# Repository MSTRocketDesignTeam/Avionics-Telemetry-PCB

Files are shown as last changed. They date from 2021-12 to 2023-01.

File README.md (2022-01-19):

View this project on [CADLAB.io](https://cadlab.io/project/24983). 

# Overview

This repository contains the PCB files for the main Rocket Telemetry project.

## Purpose and Motivation
This project aims to create flight-rated PCBs that can collect information about the team's rockets as they are launched.

The primary impetus for this project is to develop a student-designed solution to keep the team from losing rockets. This means that these boards must contain and interface with the electronics required to track and analyze a rocket mid-flight and indicate the rocket landing site location to the team back at the launch site to aid in recovery efforts.

The second purpose of this board is to collect and stream performance data about the rocket during all stages of its flight. This data will come from onboard sensors that measure the rocket’s acceleration, altitude, speed, orientation, etc. This will initially only be stored onboard the rocket, with the long-term goal of feeding a real-time 3D model simulation of the rocket’s flight to the team at the launch site. It should also be a goal to include future capabilities for interfacing with external sensors, such as thermocouples, pressure transducers, cameras, and more.

## Inspirations

Initial developments of this board are to be a direct replacement for a Telemetrum V3, with features and design optimizations to be implemented in future revisions.

A [Telemetrum V3](https://altusmetrum.org/TeleMetrum/) is an amateur rocketry telemetry solution from [Altus Metrum](https://altusmetrum.org/index.html).

[Signal](https://bps.space/signal/) from [BPS.Space](https://bps.space/) is a flight computer first and a data collection solution second. It is designed to stream data to the ground station, although it is likely insufficient for the large 10-30k ft class rockets that our team constructs.

An excellent KiCAD tutorial around making a small thumb-drive-sized PCB with an STM32, RF, and USB components: [here on YouTube by Phil's Lab](https://www.youtube.com/watch?v=14_jh3nLSsU) and is an excellent tutorial on using circuit design software and the process/approach you go through making something like this. Highly recommended to watch and maybe take some notes on. This is a solid start for our telemetry board.

# Features

#### Physical

* Expected Size: 53 x 69 mm (Arduino Uno)
* Best Size: Around 75 x 25 mm if possible
* Thin/Long is better than Square
* Rectangular shape w/ rounded edges
* Screw Mounting Holes

#### Primary Components

* STM32 Family Microcontroller
* 900MHz Radio Module
* GPS Receiver
* External RF Antenna Connector

#### Sensors

* Accelerometer
* Magnetometer
* Barometer
* Gyroscope
* Temperature

#### Data

* Flash Storage Chip for inflight capture
* Micro SD Card Reader for postflight storage
* Debugging/programming header

#### Power

* Connection to LiPo Packs
* Coin Cell/Capacitor Battery Backup
* No charge controller
* Low-power mode preflight

# Companion Documentation

[Telemetry Board R&D Documentation Folder - Google Drive](https://drive.google.com/drive/folders/1-Ft9_IYGoKeQ8SOpWUMPCNhws5y90gv3?usp=sharing)

[Component Comparison - Google Sheet](https://docs.google.com/spreadsheets/d/1QPZUW1DP2L5ciMKxbgeHV3uC0-h4SxSqm0nYhaIsA54/edit?usp=sharing)

[Telemetrum V3 Features and Components - Google Doc](https://docs.google.com/document/d/1UKlisEx7MZwDFethEzJ8d39NXyabVl6lI_5ZflczvP4/edit?usp=sharing)

[Telemetry Board Requirement Brainstorm - Google Doc](https://docs.google.com/document/d/1sqFQGxX3MVceV2B7MoNJb_ZmXdHjXhyEQbpknLjsYw0/edit?usp=sharing)

[Telemetry Notepad - Google Doc](https://docs.google.com/document/d/1K5M_XsDRmasx09W511Fg23m5dxfRa6N_FNR6dFqZZKQ/edit?usp=sharing)

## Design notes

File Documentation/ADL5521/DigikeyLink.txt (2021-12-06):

https://www.digikey.com/en/products/detail/analog-devices-inc/ADL5521ACPZ-R7/2033820

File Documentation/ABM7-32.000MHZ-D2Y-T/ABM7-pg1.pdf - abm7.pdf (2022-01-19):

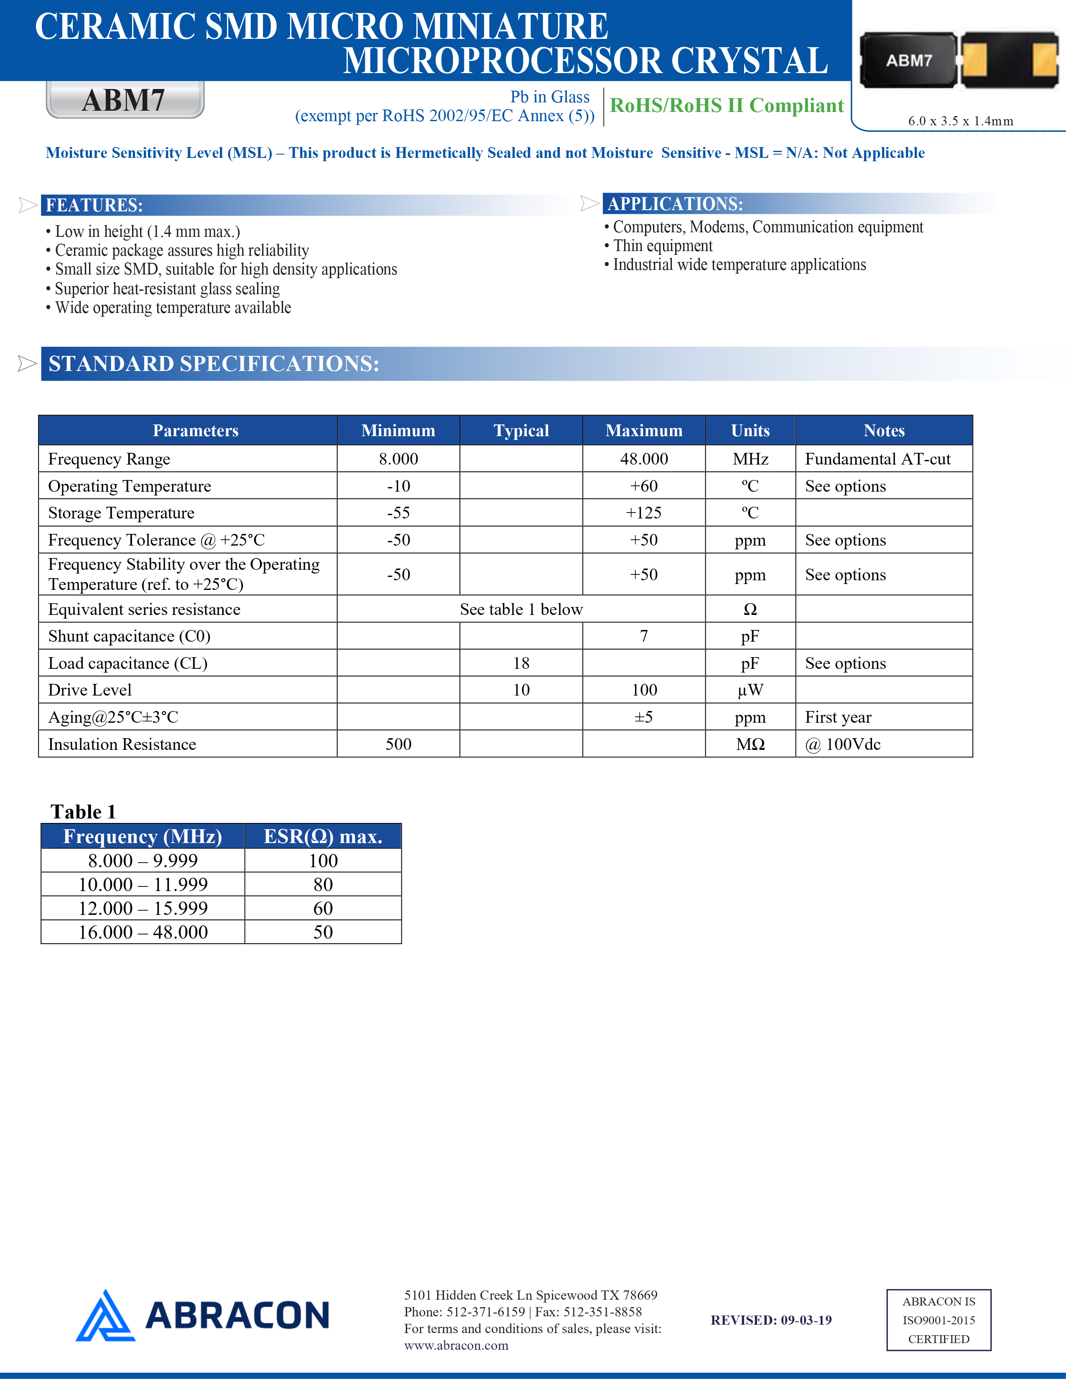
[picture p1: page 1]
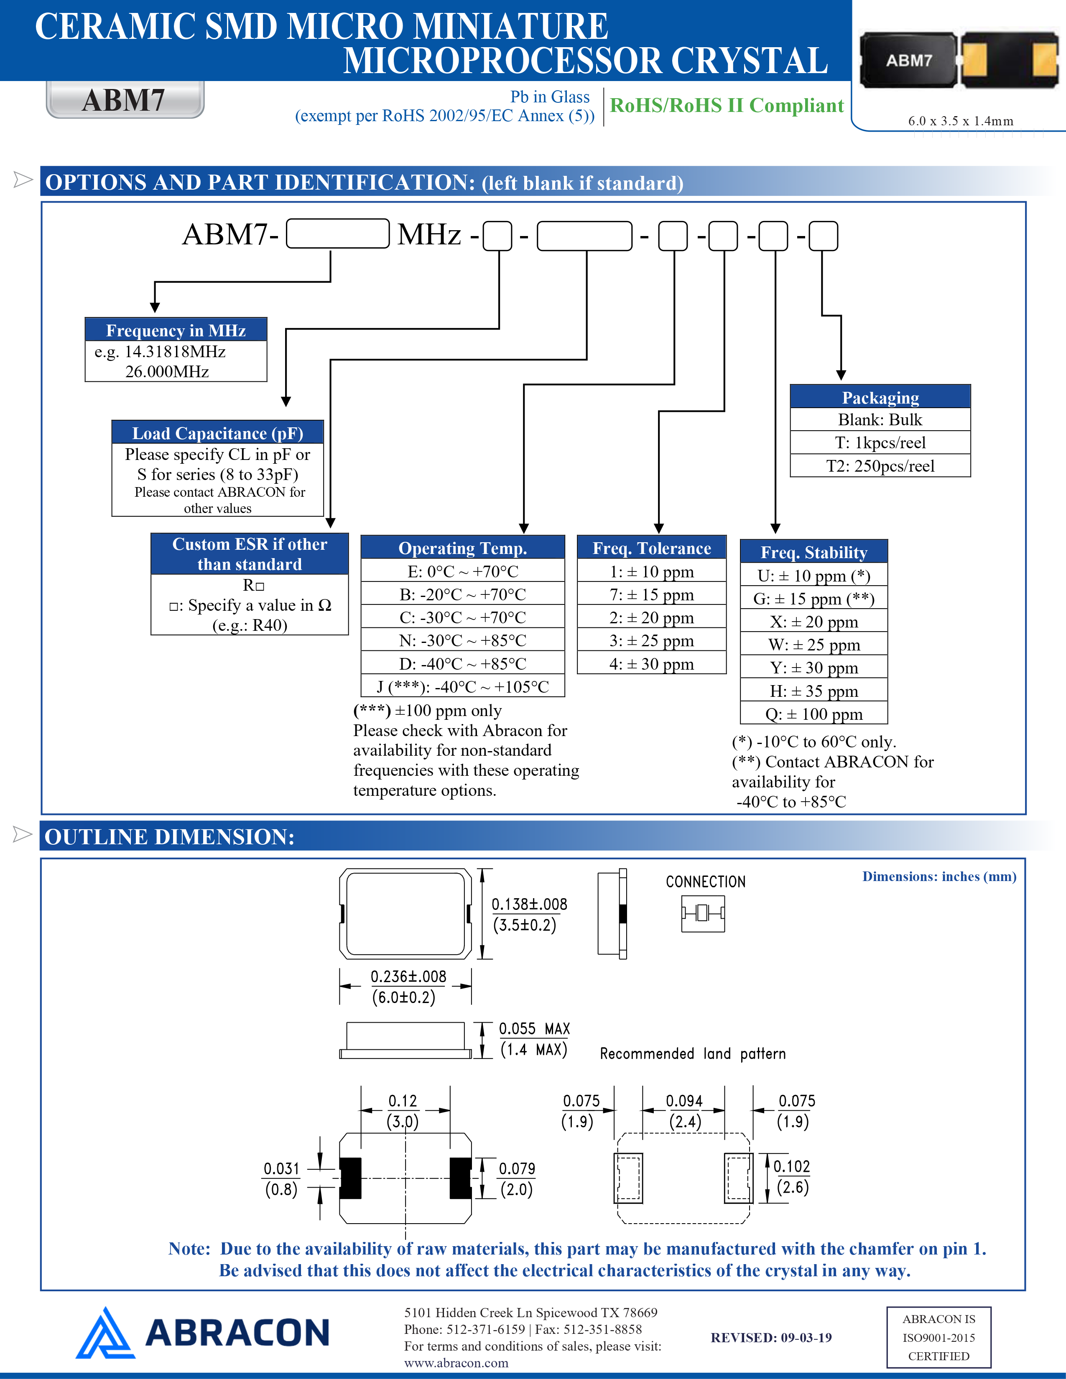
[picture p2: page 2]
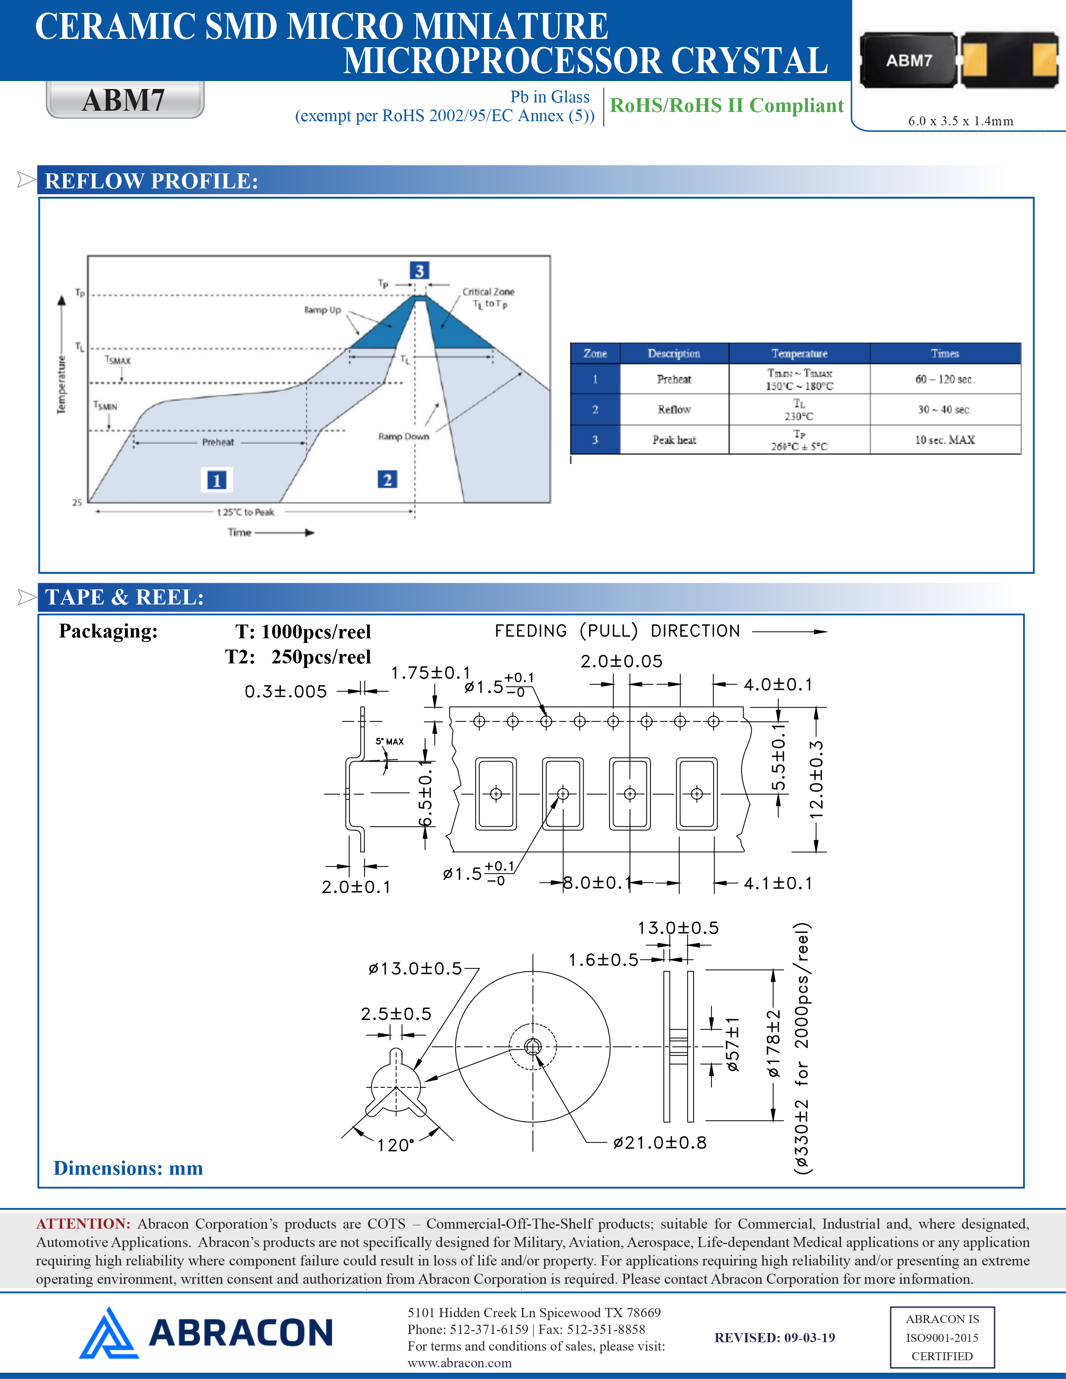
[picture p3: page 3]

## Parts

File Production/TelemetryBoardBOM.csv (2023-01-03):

Comment | Designator | Footprint | LCSC
2.4pF | C11 | Capacitor_SMD:C_0402_1005Metric | C123475
100nF | C12 | Capacitor_SMD:C_0402_1005Metric | C307331
0.1uF | C13 | Capacitor_SMD:C_0603_1608Metric_Pad1.08x0.95mm_HandSolder | C14663
100pF | C1,C3,C15,C17 | Capacitor_SMD:C_0402_1005Metric | C1546
1uF | C5,C19 | Capacitor_SMD:C_0402_1005Metric | C52923
4.7pF | C20 | Capacitor_SMD:C_0402_1005Metric | C1569
3.3pF | C21,C22 | Capacitor_SMD:C_0402_1005Metric | C1565
100nF | C23,C27,C28,C29,C30,C31,C32,C34,C35,C37 | Capacitor_SMD:C_0603_1608Metric_Pad1.08x0.95mm_HandSolder | C14663
30pF | C2,C4,C16,C18,C24,C25 | Capacitor_SMD:C_0603_1608Metric_Pad1.08x0.95mm_HandSolder | C123555
1uF | C14,C26,C33,C38 | Capacitor_SMD:C_0603_1608Metric_Pad1.08x0.95mm_HandSolder | C15849
3pF | C6 | Capacitor_SMD:C_0402_1005Metric | C115630
1pF | C7 | Capacitor_SMD:C_0402_1005Metric | C1550
DC_Blocking | C8 | Capacitor_SMD:C_0402_1005Metric | C1550
4.3pF | C9,C10 | Capacitor_SMD:C_0402_1005Metric | C159803
D_Schottky_Small | D1 | Diode_SMD:D_0805_2012Metric_Pad1.15x1.40mm_HandSolder | C22624
Red | D2,D4,D6 | LED_SMD:LED_0603_1608Metric_Pad1.05x0.95mm_HandSolder | C2286
Grn | D3,D5 | LED_SMD:LED_0603_1608Metric_Pad1.05x0.95mm_HandSolder | C434423
Ferrite_Bead_Small | FB1 | Capacitor_SMD:C_0603_1608Metric_Pad1.08x0.95mm_HandSolder | C76892
STM32L562ZET6 | IC1 | QFP50P2200X2200X160-144N | C1236660
TX SPI Debug | J1 | Connector_PinHeader_2.54mm:PinHeader_2x04_P2.54mm_Vertical | C3322532
RX SPI Debug | J2 | Connector_PinHeader_2.54mm:PinHeader_2x04_P2.54mm_Vertical | C3322532
Right Angle SMA Female | J3 | Connector_Coaxial:SMA_Molex_73251-2200_Horizontal | C3174425
609-4613-1-ND | J4 | digikeyUSBConnector:USB_Micro_B_Female_10118192 | C132564
DB37_Male_MountingHoles | J5 | RDT_Custom_Footprints:L717SDC37P1ACH4F
Debug Jumper | JP1 | Connector_PinHeader_2.54mm:PinHeader_1x03_P2.54mm_Vertical | C5346215
18nH | L1 | Inductor_SMD:L_0402_1005Metric | C24562
22nH | L2,L10 | Inductor_SMD:L_0402_1005Metric | C15178
8.2nH | L3,L4 | Inductor_SMD:L_0402_1005Metric | C16208
3.4nH | L5 | Inductor_SMD:L_0402_1005Metric | C86064
100nH | L6 | Inductor_SMD:L_0402_1005Metric | C22726
3.3nH | L7 | Inductor_SMD:L_0402_1005Metric | C86064
6.2nH | L8 | Inductor_SMD:L_0402_1005Metric | C87534
11nH | L9,L11 | Inductor_SMD:L_0402_1005Metric | C27147
1.3k | R1 | Resistor_SMD:R_0402_1005Metric | C25866
4.7k | R11,R12 | Resistor_SMD:R_0603_1608Metric_Pad0.98x0.95mm_HandSolder | C25999
240 | R2 | Resistor_SMD:R_0603_1608Metric_Pad0.98x0.95mm_HandSolder | C23350
390 | R3 | Resistor_SMD:R_0603_1608Metric_Pad0.98x0.95mm_HandSolder | C23151
4.7k | R4,R5 | Resistor_SMD:R_0603_1608Metric_Pad1.05x0.95mm_HandSolder | C25999
820 | R6,R7,R8,R9,R10 | Resistor_SMD:R_0603_1608Metric_Pad1.05x0.95mm_HandSolder | C23253
MCU Reset | SW1 | Button_Switch_SMD:SW_SPST_PTS645 | C2837531
ADL5521 | U2 | Package_CSP:LFCSP-8-1EP_3x3mm_P0.5mm_EP1.45x1.74mm | C657768
RSD-897.500-942.500-1612-TR | U3 | RDT_Custom_Footprints:RSD-897.500-942.500-1612-TR | C3271762
LP38692MPX-ADJ | U4 | Package_TO_SOT_SMD:SOT-223-5 | C527485
USBLC6-2SC6 | U5 | Package_TO_SOT_SMD:SOT-23-6 | C7519
Si4463 | U1,U6 | Package_DFN_QFN:QFN-20-1EP_4x4mm_P0.5mm_EP2.6x2.6mm_ThermalVias | C476202
32MHz | Y1,Y2,Y3 | RDT_Custom_Footprints:XTAL_ABM7-32.000MHZ-D2Y-T | C1986810

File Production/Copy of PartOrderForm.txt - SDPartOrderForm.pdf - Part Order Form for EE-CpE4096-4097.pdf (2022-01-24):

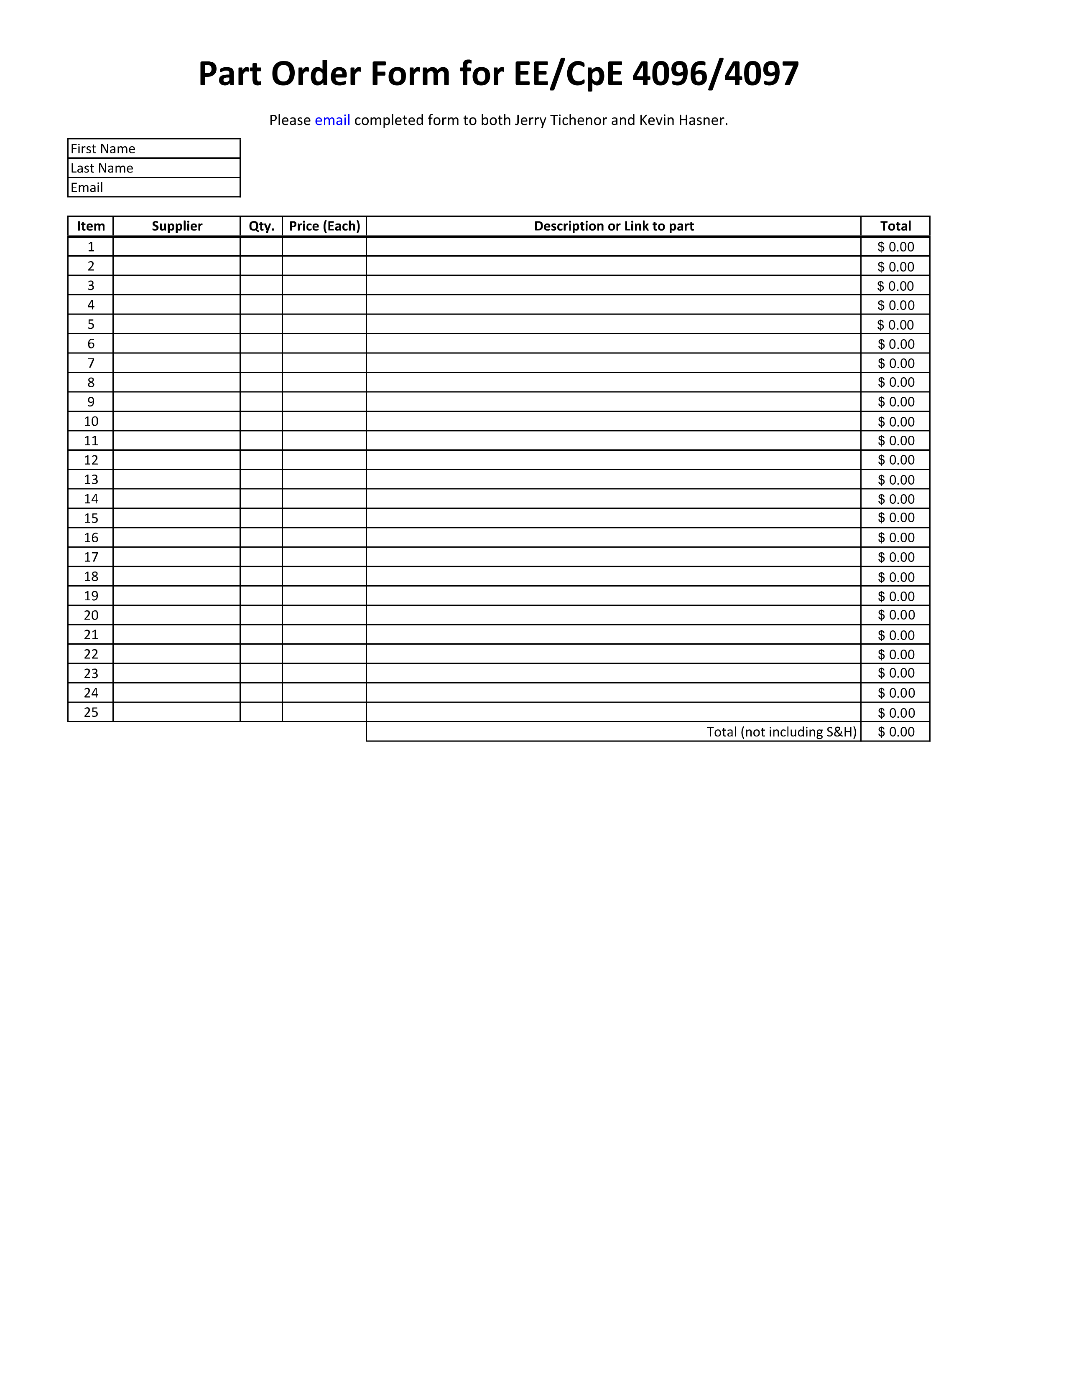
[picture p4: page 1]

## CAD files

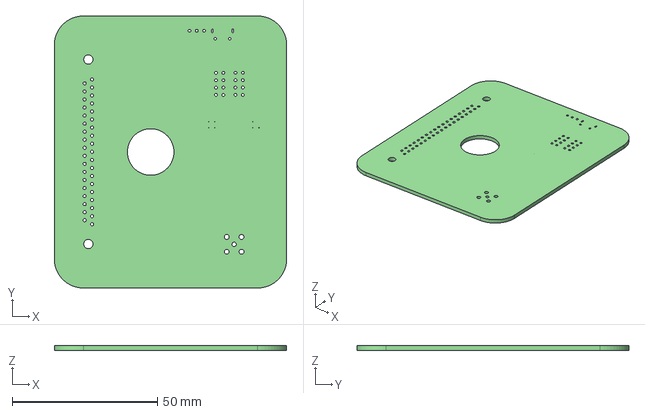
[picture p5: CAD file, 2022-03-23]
Hardware/Telemetry_KiCAD_Project_Corrected_Dimensions.step
80.0 x 93.6 x 1.60 mm

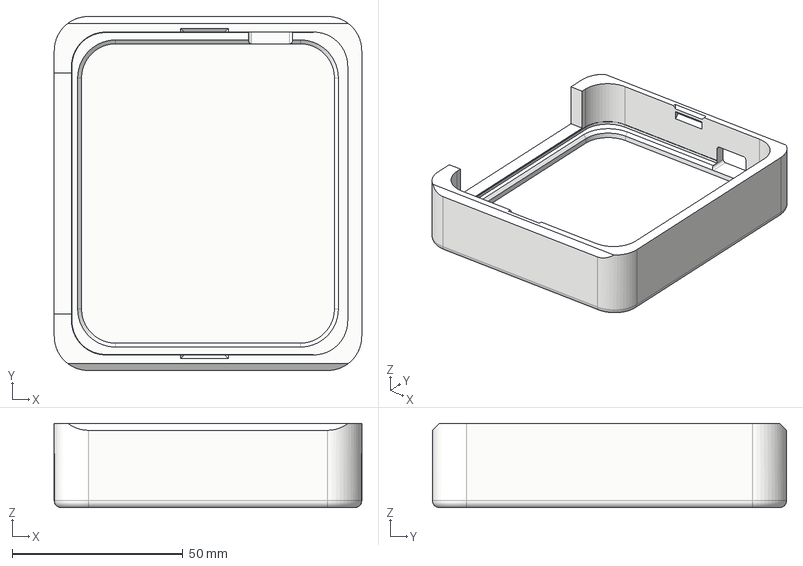
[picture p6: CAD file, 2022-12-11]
Production/PCB_Case_Body.step
90.0 x 103.6 x 24.6 mm

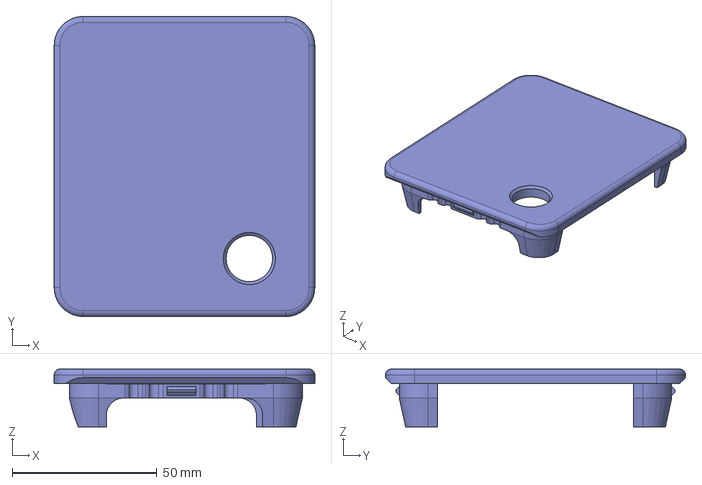
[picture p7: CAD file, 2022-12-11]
Production/PCB_Case_Top.step
90.0 x 103.6 x 20.0 mm

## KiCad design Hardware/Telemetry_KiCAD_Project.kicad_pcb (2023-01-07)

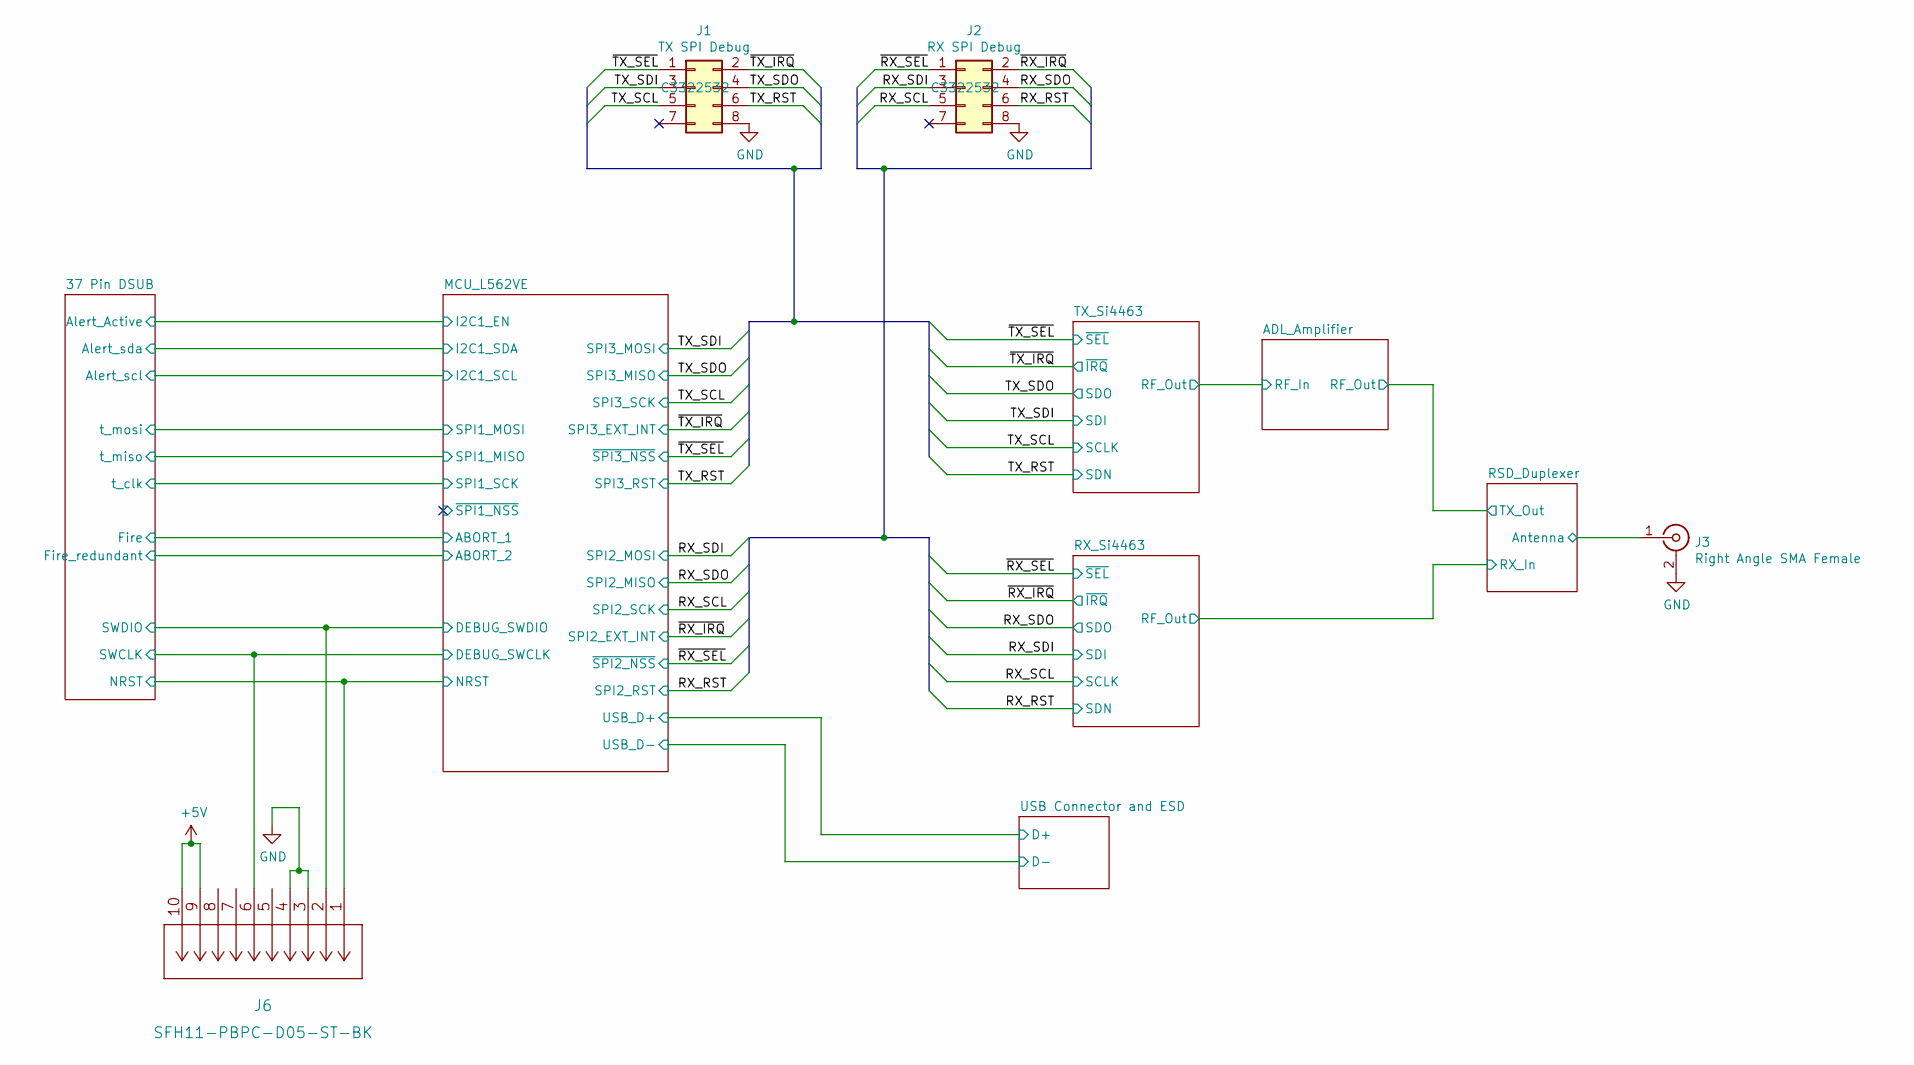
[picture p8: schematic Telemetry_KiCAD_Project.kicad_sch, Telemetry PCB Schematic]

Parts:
J1: TX SPI Debug; PinHeader_2x04_P2.54mm_Vertical; LCSC C3322532
J2: RX SPI Debug; PinHeader_2x04_P2.54mm_Vertical; LCSC C3322532
J3: Right Angle SMA Female; SMA_Molex_73251-2200_Horizontal; LCSC C3174425
J6: SFH11-PBPC-D05-ST-BK

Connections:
+5V: J6.9, J6.10; also elsewhere on the board
/37 Pin DSUB/SWCLK: J6.6; also elsewhere on the board
/37 Pin DSUB/SWDIO: J6.2; also elsewhere on the board
/MCU_L562VE/~RESET: J6.1; also elsewhere on the board
/RSD_Duplexer/Antenna: J3.1 (In); also elsewhere on the board
/RX_RST: J2.6; also elsewhere on the board
/RX_SCL: J2.5; also elsewhere on the board
/RX_SDI: J2.3; also elsewhere on the board
/RX_SDO: J2.4; also elsewhere on the board
/TX_RST: J1.6; also elsewhere on the board
/TX_SCL: J1.5; also elsewhere on the board
/TX_SDI: J1.3; also elsewhere on the board
/TX_SDO: J1.4; also elsewhere on the board
/~RX_IRQ: J2.2; also elsewhere on the board
/~RX_SEL: J2.1; also elsewhere on the board
/~TX_IRQ: J1.2; also elsewhere on the board
/~TX_SEL: J1.1; also elsewhere on the board
GND: J1.8, J2.8, J3.2 (Ext), J6.3, J6.4; also elsewhere on the board

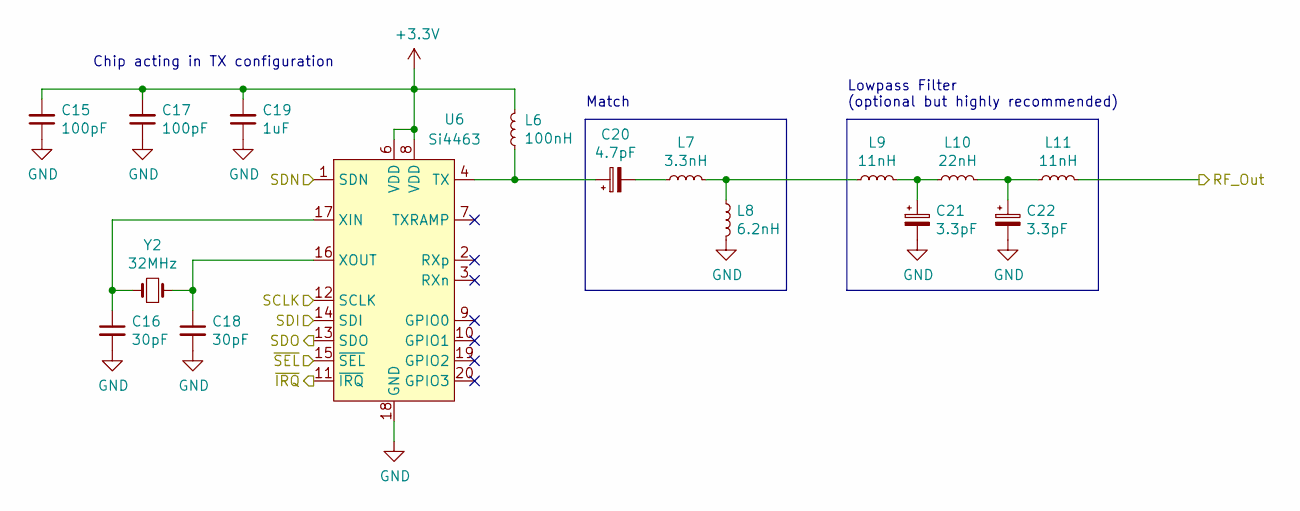
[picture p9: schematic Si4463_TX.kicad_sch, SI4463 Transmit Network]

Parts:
C15, C17: 100pF; C_0402_1005Metric; LCSC C1546
C16, C18: 30pF; C_0603_1608Metric_Pad1.08x0.95mm_HandSolder; LCSC C123555
C19: 1uF; C_0402_1005Metric; LCSC C52923
C20: 4.7pF; C_0402_1005Metric; LCSC C1569
C21, C22: 3.3pF; C_0402_1005Metric; LCSC C1565
L6: 100nH; L_0402_1005Metric; LCSC C22726
L7: 3.3nH; L_0402_1005Metric; LCSC C86064
L8: 6.2nH; L_0402_1005Metric; LCSC C87534
L9, L11: 11nH; L_0402_1005Metric; LCSC C27147
L10: 22nH; L_0402_1005Metric; LCSC C15178
U6: Si4463; QFN-20-1EP_4x4mm_P0.5mm_EP2.6x2.6mm_ThermalVias; LCSC C476202
Y2: 32MHz; XTAL_ABM7-32.000MHZ-D2Y-T; LCSC C1986810

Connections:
+3V3: C15.2, C17.2, C19.2, L6.2, U6.6 (VDD), U6.8 (VDD); also elsewhere on the board
/ADL_Amplifier/RF_In: L11.2; also elsewhere on the board
/TX_RST: U6.1 (SDN); also elsewhere on the board
/TX_SCL: U6.12 (SCLK); also elsewhere on the board
/TX_SDI: U6.14 (SDI); also elsewhere on the board
/TX_SDO: U6.13 (SDO); also elsewhere on the board
/~TX_IRQ: U6.11 (~IRQ); also elsewhere on the board
/~TX_SEL: U6.15 (~SEL); also elsewhere on the board
GND: C15.1, C16.2, C17.1, C18.2, C19.1, C21.2, C22.2, L8.2, U6.18 (GND), U6.21 (GND); also elsewhere on the board
unnamed: C16.1, U6.17 (XIN), Y2.1
unnamed: C18.1, U6.16 (XOUT), Y2.2
unnamed: C20.1, L6.1, U6.4 (TX)
unnamed: C20.2, L7.1
unnamed: C21.1, L9.2, L10.1
unnamed: C22.1, L10.2, L11.1
unnamed: L7.2, L8.1, L9.1

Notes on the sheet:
Match
Chip acting in TX configuration
Lowpass Filter (optional but highly recommended)

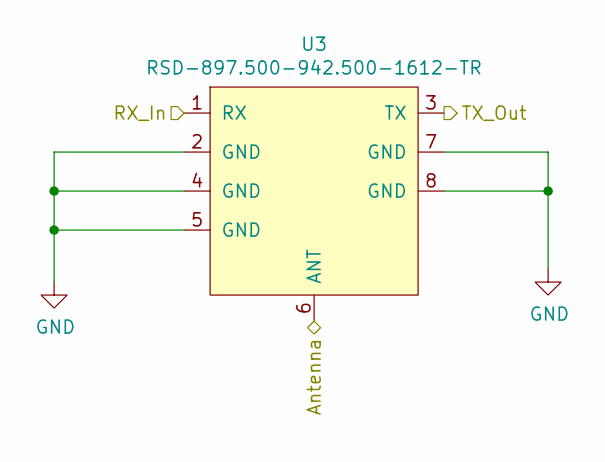
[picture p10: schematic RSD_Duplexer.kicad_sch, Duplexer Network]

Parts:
U3: RSD-897.500-942.500-1612-TR; LCSC C3271762

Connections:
/ADL_Amplifier/RF_Out: U3.3 (TX); also elsewhere on the board
/RSD_Duplexer/Antenna: U3.6 (ANT); also elsewhere on the board
/RSD_Duplexer/RX_In: U3.1 (RX); also elsewhere on the board
GND: U3.2 (GND), U3.4 (GND), U3.5 (GND), U3.7 (GND), U3.8 (GND); also elsewhere on the board

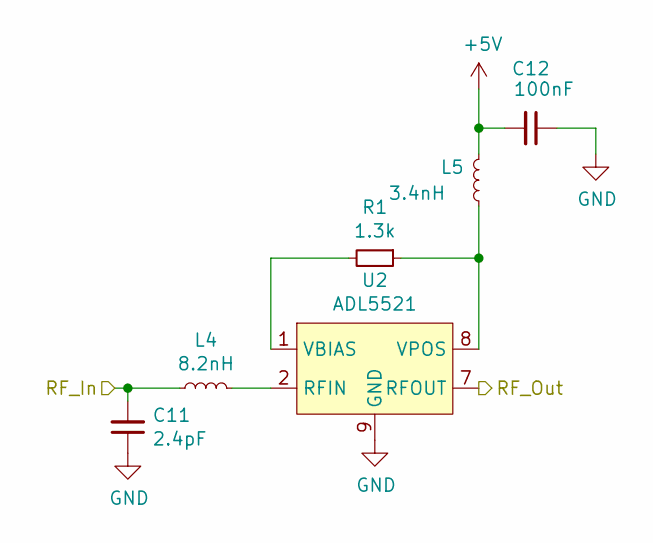
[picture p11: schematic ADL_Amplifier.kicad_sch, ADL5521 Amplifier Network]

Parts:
C11: 2.4pF; C_0402_1005Metric; LCSC C123475
C12: 100nF; C_0402_1005Metric; LCSC C307331
L4: 8.2nH; L_0402_1005Metric; LCSC C16208
L5: 3.4nH; L_0402_1005Metric; LCSC C86064
R1: 1.3k; R_0402_1005Metric; LCSC C25866
U2: ADL5521; LFCSP-8-1EP_3x3mm_P0.5mm_EP1.45x1.74mm; LCSC C657768

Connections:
+5V: C12.2, L5.2; also elsewhere on the board
/ADL_Amplifier/RF_In: C11.2, L4.1; also elsewhere on the board
/ADL_Amplifier/RF_Out: U2.7 (RFOUT); also elsewhere on the board
GND: C11.1, C12.1, U2.9 (GND); also elsewhere on the board
unnamed: L4.2, U2.2 (RFIN)
unnamed: L5.1, R1.1, U2.8 (VPOS)
unnamed: R1.2, U2.1 (VBIAS)

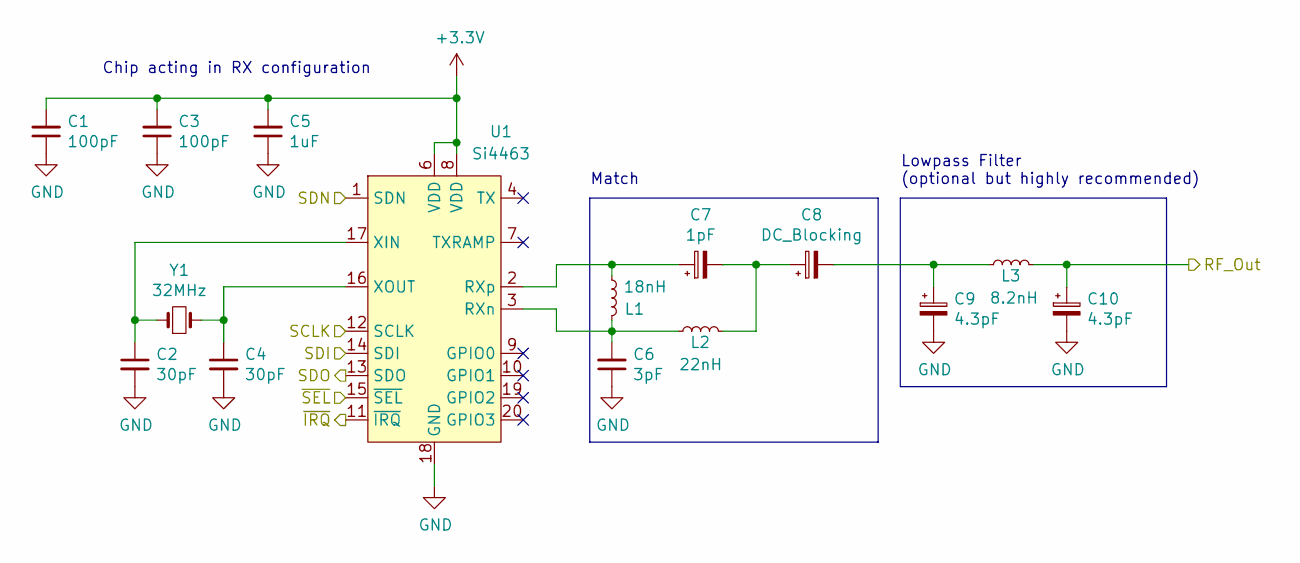
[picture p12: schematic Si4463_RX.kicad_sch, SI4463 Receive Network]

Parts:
C1, C3: 100pF; C_0402_1005Metric; LCSC C1546
C2, C4: 30pF; C_0603_1608Metric_Pad1.08x0.95mm_HandSolder; LCSC C123555
C5: 1uF; C_0402_1005Metric; LCSC C52923
C6: 3pF; C_0402_1005Metric; LCSC C115630
C7: 1pF; C_0402_1005Metric; LCSC C1550
C8: DC_Blocking; C_0402_1005Metric; LCSC C1550
C9, C10: 4.3pF; C_0402_1005Metric; LCSC C159803
L1: 18nH; L_0402_1005Metric; LCSC C24562
L2: 22nH; L_0402_1005Metric; LCSC C15178
L3: 8.2nH; L_0402_1005Metric; LCSC C16208
U1: Si4463; QFN-20-1EP_4x4mm_P0.5mm_EP2.6x2.6mm_ThermalVias; LCSC C476202
Y1: 32MHz; XTAL_ABM7-32.000MHZ-D2Y-T; LCSC C1986810

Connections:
+3V3: C1.2, C3.2, C5.2, U1.6 (VDD), U1.8 (VDD); also elsewhere on the board
/RSD_Duplexer/RX_In: C10.1, L3.2; also elsewhere on the board
/RX_RST: U1.1 (SDN); also elsewhere on the board
/RX_SCL: U1.12 (SCLK); also elsewhere on the board
/RX_SDI: U1.14 (SDI); also elsewhere on the board
/RX_SDO: U1.13 (SDO); also elsewhere on the board
/~RX_IRQ: U1.11 (~IRQ); also elsewhere on the board
/~RX_SEL: U1.15 (~SEL); also elsewhere on the board
GND: C1.1, C2.2, C3.1, C4.2, C5.1, C6.1, C9.2, C10.2, U1.18 (GND), U1.21 (GND); also elsewhere on the board
unnamed: C2.1, U1.17 (XIN), Y1.1
unnamed: C4.1, U1.16 (XOUT), Y1.2
unnamed: C6.2, L1.2, L2.1, U1.3 (RXn)
unnamed: C7.1, L1.1, U1.2 (RXp)
unnamed: C7.2, C8.1, L2.2
unnamed: C8.2, C9.1, L3.1

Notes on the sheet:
Chip acting in RX configuration
Lowpass Filter (optional but highly recommended)
Match

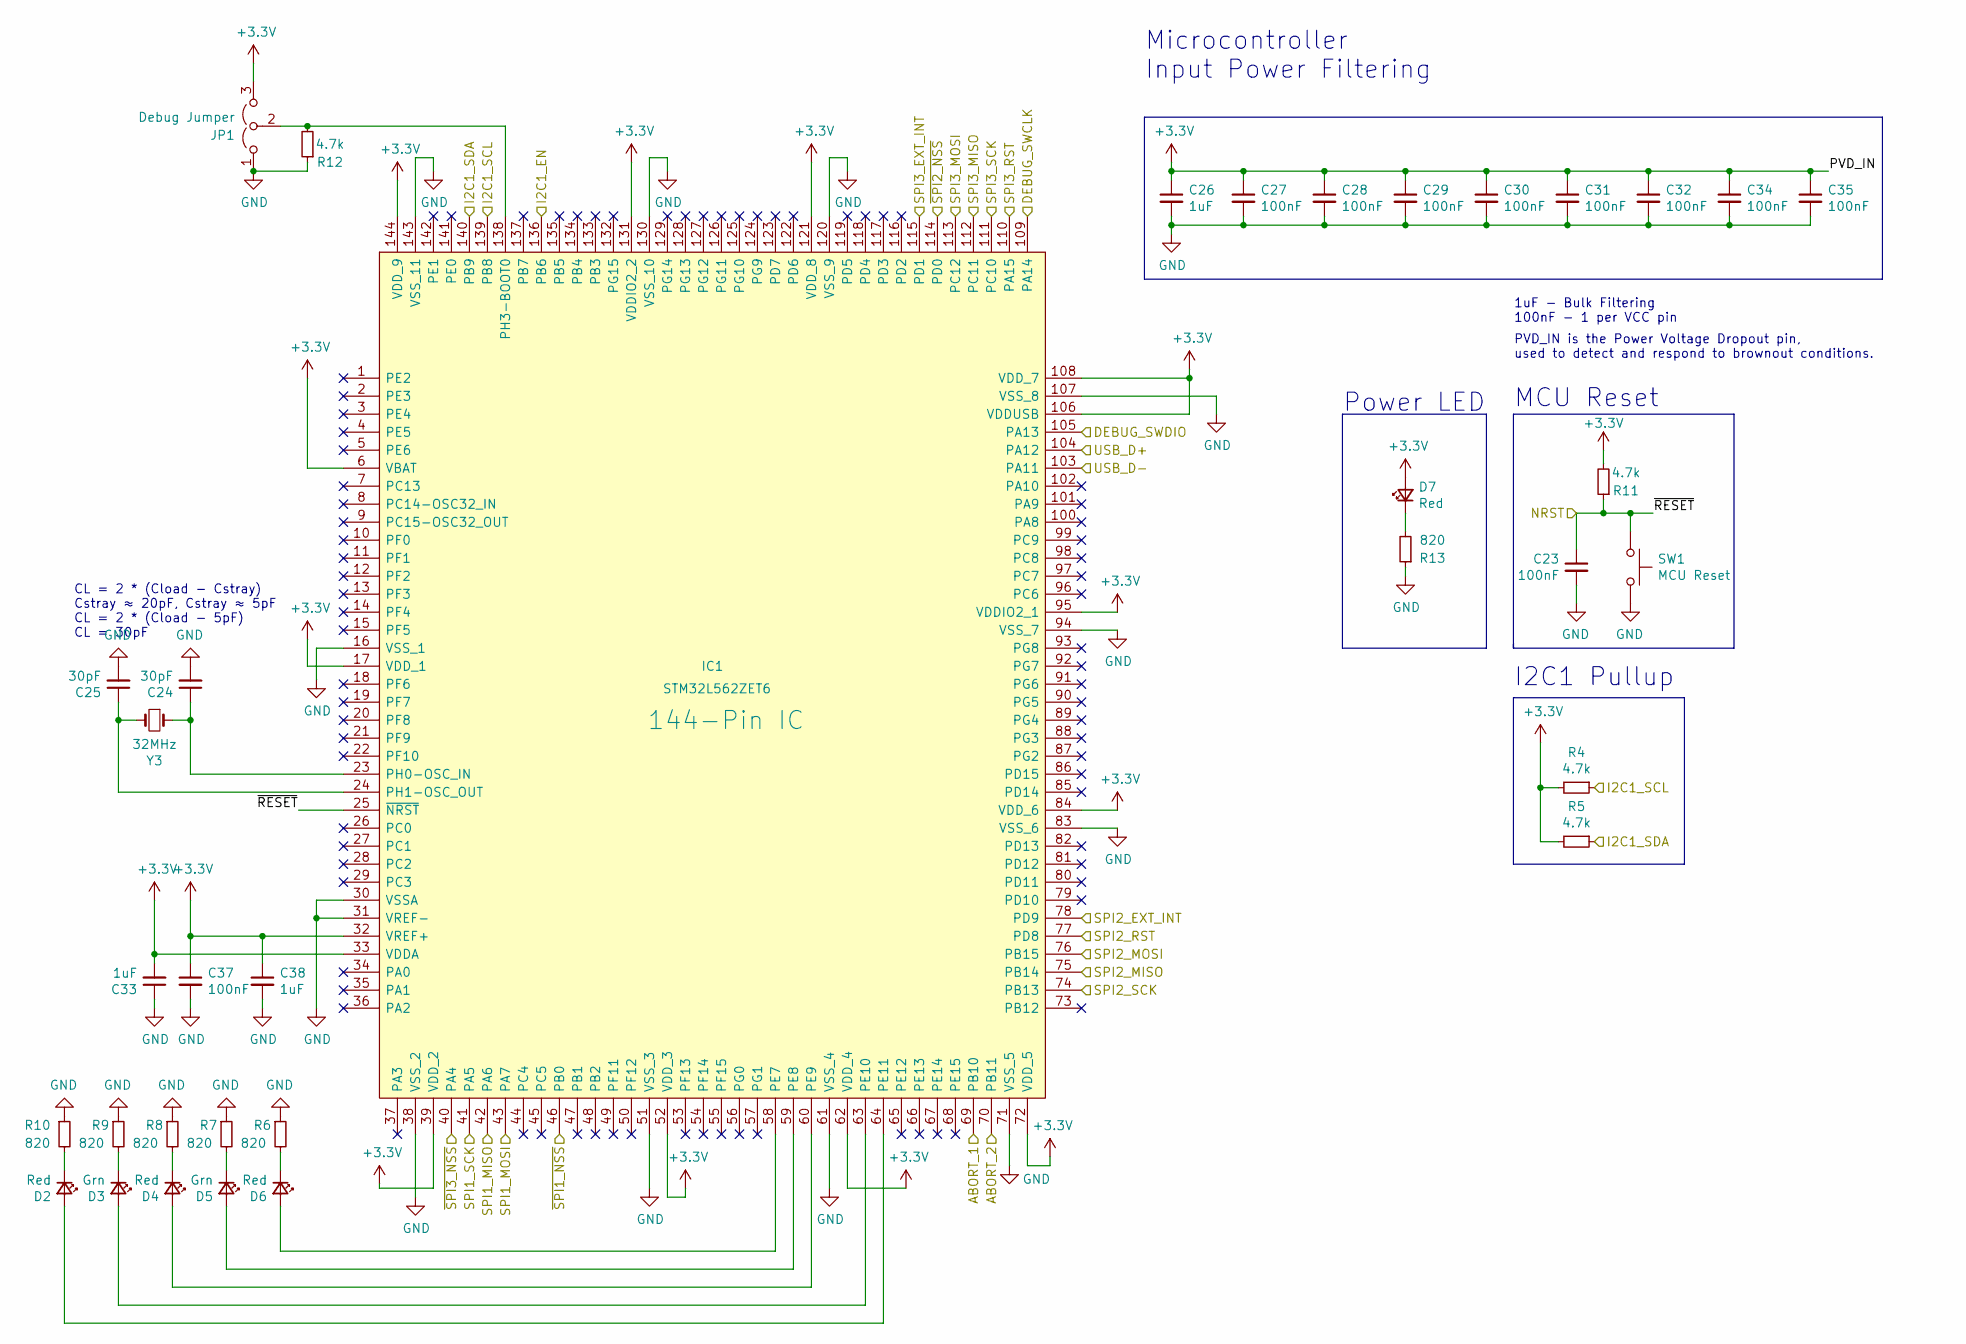
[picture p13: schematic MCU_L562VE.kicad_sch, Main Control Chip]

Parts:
C23, C27, C28, C29, C30, C31, C32, C34, C35, C37: 100nF; C_0603_1608Metric_Pad1.08x0.95mm_HandSolder; LCSC C14663
C24, C25: 30pF; C_0603_1608Metric_Pad1.08x0.95mm_HandSolder; LCSC C123555
C26: 1uF; C_0603_1608Metric_Pad1.08x0.95mm_HandSolder; LCSC C15849
C33, C38: 1uF; C_0603_1608Metric_Pad1.08x0.95mm_HandSolder; LCSC C14663
D2, D4, D6, D7: Red; LED_0603_1608Metric_Pad1.05x0.95mm_HandSolder; LCSC C2286
D3, D5: Grn; LED_0603_1608Metric_Pad1.05x0.95mm_HandSolder; LCSC C434423
IC1: STM32L562ZET6; QFP50P2200X2200X160-144N; Mouser Part Number 511-STM32L562ZET6
JP1: Debug Jumper; PinHeader_1x03_P2.54mm_Vertical; LCSC C5346215
R4, R5: 4.7k; R_0603_1608Metric_Pad1.05x0.95mm_HandSolder; LCSC C25999
R6, R7, R8, R9, R10: 820; R_0603_1608Metric_Pad1.05x0.95mm_HandSolder; LCSC C23253
R11, R12: 4.7k; R_0603_1608Metric_Pad0.98x0.95mm_HandSolder; LCSC C25999
R13: 820; R_0603_1608Metric; LCSC C23253
SW1: MCU Reset; SW_SPST_PTS645; LCSC C2837531
Y3: 32MHz; XTAL_ABM7-32.000MHZ-D2Y-T; LCSC C1986810

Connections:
+3V3: C26.1, C27.1, C28.1, C29.1, C30.1, C31.1, C32.1, C33.2, C34.1, C35.1, C37.1, C38.1, D7.2 (A), IC1.6 (VBAT), IC1.17 (VDD_1), IC1.32 (VREF+), IC1.33 (VDDA), IC1.39 (VDD_2), IC1.52 (VDD_3), IC1.62 (VDD_4), IC1.72 (VDD_5), IC1.84 (VDD_6), IC1.95 (VDDIO2_1), IC1.106 (VDDUSB), IC1.108 (VDD_7), IC1.121 (VDD_8), IC1.131 (VDDIO2_2), IC1.144 (VDD_9), JP1.3 (B), R4.2, R5.2, R11.2; also elsewhere on the board
/37 Pin DSUB/Alert_Active: IC1.136 (PB6); also elsewhere on the board
/37 Pin DSUB/Alert_scl: IC1.139 (PB8), R4.1; also elsewhere on the board
/37 Pin DSUB/Alert_sda: IC1.140 (PB9), R5.1; also elsewhere on the board
/37 Pin DSUB/Fire: IC1.69 (PB10); also elsewhere on the board
/37 Pin DSUB/Fire_redundant: IC1.70 (PB11); also elsewhere on the board
/37 Pin DSUB/SWCLK: IC1.109 (PA14); also elsewhere on the board
/37 Pin DSUB/SWDIO: IC1.105 (PA13); also elsewhere on the board
/37 Pin DSUB/t_clk: IC1.41 (PA5); also elsewhere on the board
/37 Pin DSUB/t_miso: IC1.42 (PA6); also elsewhere on the board
/37 Pin DSUB/t_mosi: IC1.43 (PA7); also elsewhere on the board
/MCU_L562VE/USB_D+: IC1.104 (PA12); also elsewhere on the board
/MCU_L562VE/USB_D-: IC1.103 (PA11); also elsewhere on the board
/MCU_L562VE/~RESET: C23.1, IC1.25 (~NRST), R11.1, SW1.1; also elsewhere on the board
/MCU_L562VE/~SPI1_NSS: IC1.46 (PB0)
/RX_RST: IC1.77 (PD8); also elsewhere on the board
/RX_SCL: IC1.74 (PB13); also elsewhere on the board
/RX_SDI: IC1.76 (PB15); also elsewhere on the board
/RX_SDO: IC1.75 (PB14); also elsewhere on the board
/TX_RST: IC1.110 (PA15); also elsewhere on the board
/TX_SCL: IC1.111 (PC10); also elsewhere on the board
/TX_SDI: IC1.113 (PC12); also elsewhere on the board
/TX_SDO: IC1.112 (PC11); also elsewhere on the board
/~RX_IRQ: IC1.78 (PD9); also elsewhere on the board
/~RX_SEL: IC1.114 (PD0); also elsewhere on the board
/~TX_IRQ: IC1.115 (PD1); also elsewhere on the board
/~TX_SEL: IC1.40 (PA4); also elsewhere on the board
GND: C23.2, C24.2, C25.2, C26.2, C27.2, C28.2, C29.2, C30.2, C31.2, C32.2, C33.1, C34.2, C35.2, C37.2, C38.2, IC1.16 (VSS_1), IC1.30 (VSSA), IC1.31 (VREF-), IC1.38 (VSS_2), IC1.51 (VSS_3), IC1.61 (VSS_4), IC1.71 (VSS_5), IC1.83 (VSS_6), IC1.94 (VSS_7), IC1.107 (VSS_8), IC1.120 (VSS_9), IC1.130 (VSS_10), IC1.143 (VSS_11), JP1.1 (A), R6.1, R7.1, R8.1, R9.1, R10.1, R12.1, R13.1, SW1.2; also elsewhere on the board
unnamed: C24.1, IC1.23 (PH0-OSC_IN), Y3.1
unnamed: C25.1, IC1.24 (PH1-OSC_OUT), Y3.2
unnamed: D2.1 (K), R10.2
unnamed: D2.2 (A), IC1.64 (PE11)
unnamed: D3.1 (K), R9.2
unnamed: D3.2 (A), IC1.63 (PE10)
unnamed: D4.1 (K), R8.2
unnamed: D4.2 (A), IC1.60 (PE9)
unnamed: D5.1 (K), R7.2
unnamed: D5.2 (A), IC1.59 (PE8)
unnamed: D6.1 (K), R6.2
unnamed: D6.2 (A), IC1.58 (PE7)
unnamed: D7.1 (K), R13.2
unnamed: IC1.138 (PH3-BOOT0), JP1.2 (C), R12.2

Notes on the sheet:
Microcontroller Input Power Filtering
I2C1 Pullup
MCU Reset
PVD_IN is the Power Voltage Dropout pin, used to detect and respond to brownout conditions.
1uF - Bulk Filtering 100nF - 1 per VCC pin
Power LED
CL = 2 * (Cload - Cstray) Cstray ≈ 20pF, Cstray ≈ 5pF CL = 2 * (Cload - 5pF) CL = 30pF

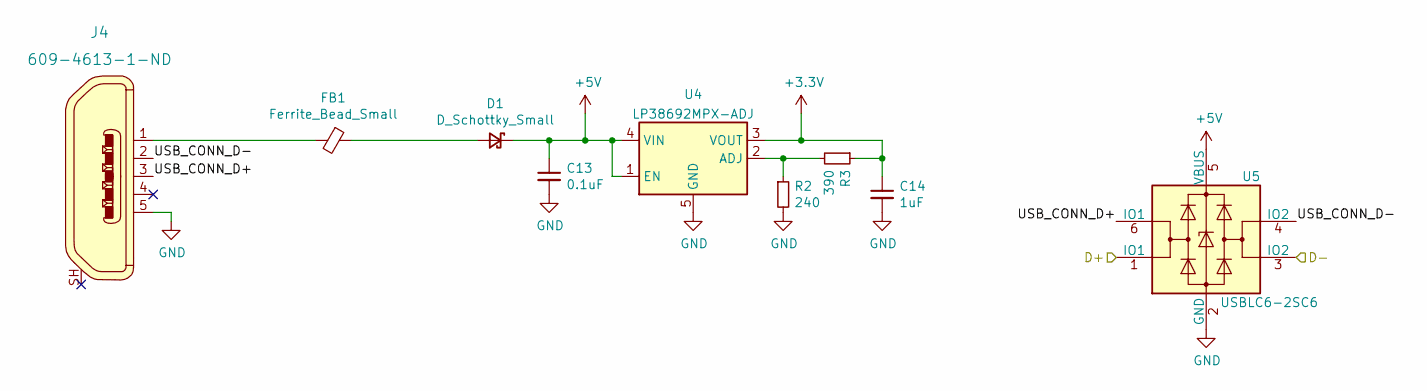
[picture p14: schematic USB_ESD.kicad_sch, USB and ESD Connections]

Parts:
C13: 0.1uF; C_0603_1608Metric_Pad1.08x0.95mm_HandSolder; LCSC C14663
C14: 1uF; C_0603_1608Metric_Pad1.08x0.95mm_HandSolder; LCSC C15849
D1: D_Schottky_Small; D_0805_2012Metric_Pad1.15x1.40mm_HandSolder; LCSC C22624
FB1: Ferrite_Bead_Small; C_0603_1608Metric_Pad1.08x0.95mm_HandSolder; LCSC C76892
J4: 609-4613-1-ND; USB_Micro_B_Female_10118192; LCSC C132564
R2: 240; R_0603_1608Metric_Pad0.98x0.95mm_HandSolder; LCSC C23350
R3: 390; R_0603_1608Metric_Pad0.98x0.95mm_HandSolder; LCSC C23151
U4: LP38692MPX-ADJ; SOT-223-5; LCSC C527485
U5: USBLC6-2SC6; SOT-23-6; LCSC C7519

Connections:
+3V3: C14.1, R3.1, U4.3 (VOUT); also elsewhere on the board
+5V: C13.1, D1.1 (K), U4.1 (EN), U4.4 (VIN), U5.5 (VBUS); also elsewhere on the board
/MCU_L562VE/USB_D+: U5.1 (IO1); also elsewhere on the board
/MCU_L562VE/USB_D-: U5.3 (IO2); also elsewhere on the board
/USB Connector and ESD/USB_CONN_D+: J4.3, U5.6 (IO1)
/USB Connector and ESD/USB_CONN_D-: J4.2, U5.4 (IO2)
GND: C13.2, C14.2, J4.5, R2.2, U4.5 (GND), U5.2 (GND); also elsewhere on the board
unnamed: D1.2 (A), FB1.1
unnamed: FB1.2, J4.1
unnamed: R2.1, R3.2, U4.2 (ADJ)

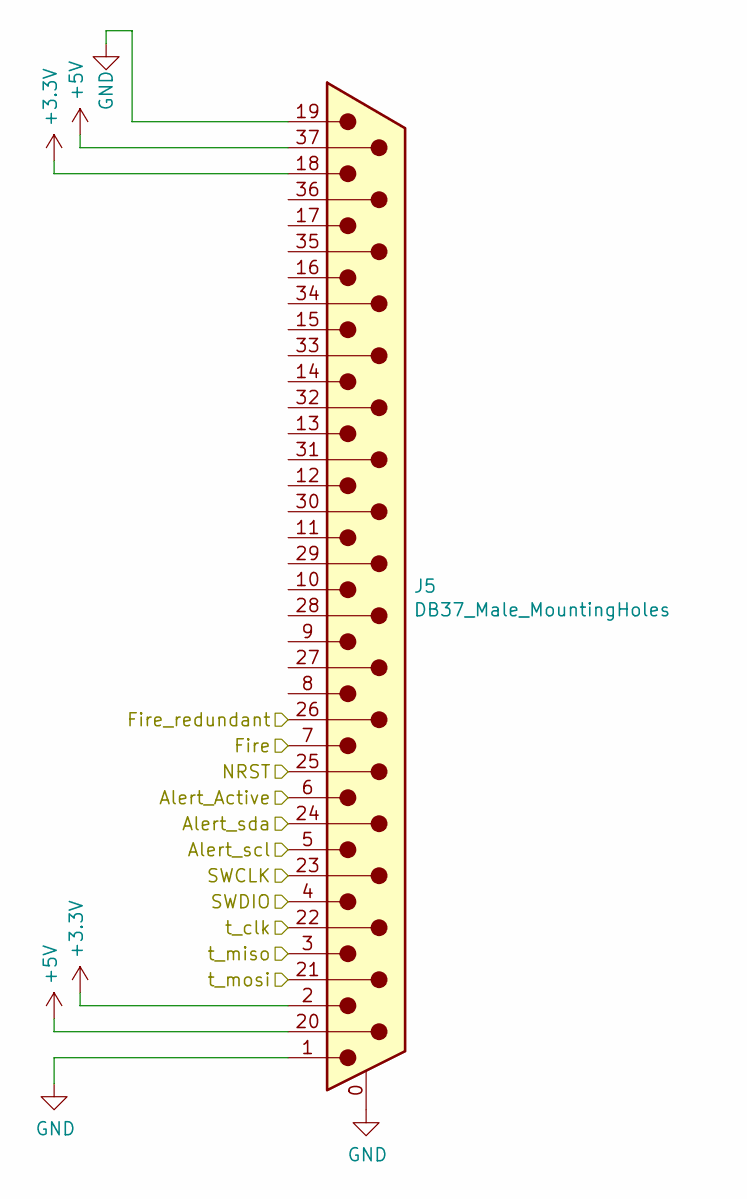
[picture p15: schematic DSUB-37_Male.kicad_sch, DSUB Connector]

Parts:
J5: DB37_Male_MountingHoles; L717SDC37P1ACH4F

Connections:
+3V3: J5.2, J5.18; also elsewhere on the board
+5V: J5.20, J5.37; also elsewhere on the board
/37 Pin DSUB/Alert_Active: J5.6; also elsewhere on the board
/37 Pin DSUB/Alert_scl: J5.5; also elsewhere on the board
/37 Pin DSUB/Alert_sda: J5.24; also elsewhere on the board
/37 Pin DSUB/Fire: J5.7; also elsewhere on the board
/37 Pin DSUB/Fire_redundant: J5.26; also elsewhere on the board
/37 Pin DSUB/SWCLK: J5.23; also elsewhere on the board
/37 Pin DSUB/SWDIO: J5.4; also elsewhere on the board
/37 Pin DSUB/t_clk: J5.22; also elsewhere on the board
/37 Pin DSUB/t_miso: J5.3; also elsewhere on the board
/37 Pin DSUB/t_mosi: J5.21; also elsewhere on the board
/MCU_L562VE/~RESET: J5.25; also elsewhere on the board
GND: J5.0 (PAD), J5.1, J5.19; also elsewhere on the board

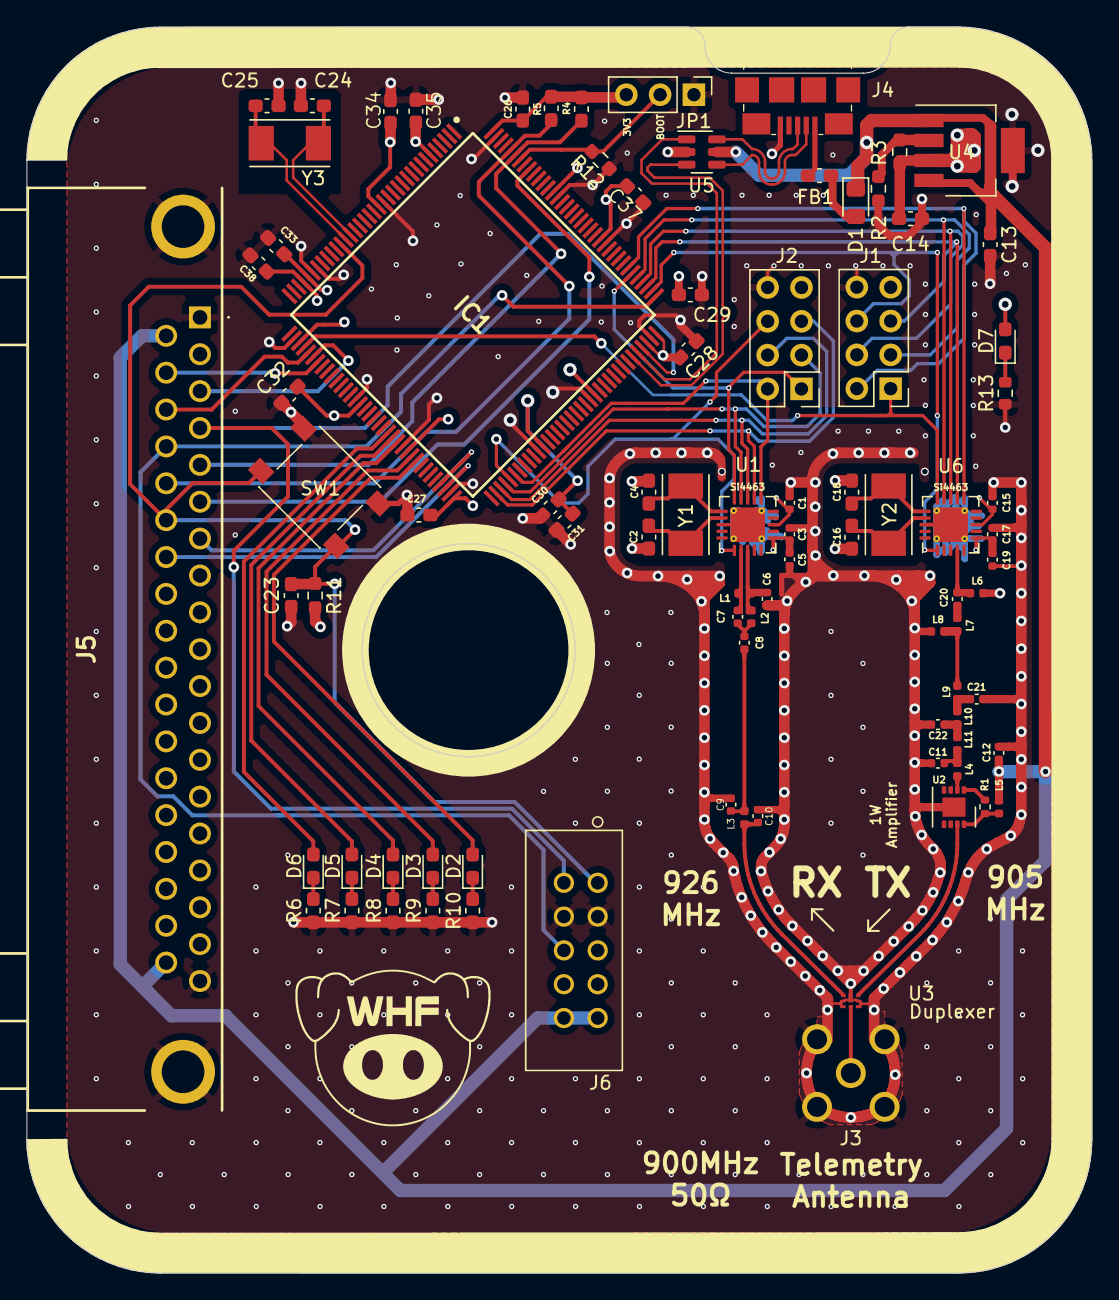
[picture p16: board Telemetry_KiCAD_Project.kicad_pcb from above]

Board: 4 copper layers, 80.0 x 93.6 mm, 87 parts (0 on the bottom side), 67 nets.

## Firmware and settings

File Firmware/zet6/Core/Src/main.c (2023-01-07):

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
/* Includes ------------------------------------------------------------------*/
#include "main.h"

/* USER CODE BEGIN Includes */
#include <stdio.h>
/* USER CODE END Includes */


SPI_HandleTypeDef hspi2;
SPI_HandleTypeDef hspi3;

PCD_HandleTypeDef hpcd_USB_FS;

void SystemClock_Config(void);
static void MX_GPIO_Init(void);
static void MX_ICACHE_Init(void);
static void MX_USB_PCD_Init(void);
static void MX_SPI2_Init(void);
static void MX_SPI3_Init(void);
/* USER CODE BEGIN 0 */
//HAL_SPI_Transmit(&hspi2, )
/* USER CODE END 0 */

/**
  * @brief  The application entry point.
  * @retval int
  */
int main(void)
{
  /* USER CODE BEGIN 1 */
  char spi_buf[20] = {0};
  /* USER CODE END 1 */

  /* MCU Configuration--------------------------------------------------------*/

  /* Reset of all peripherals, Initializes the Flash interface and the Systick. */
  HAL_Init();

  /* Configure the system clock */
  SystemClock_Config();

  /* Initialize all configured peripherals */
  MX_GPIO_Init();
  MX_ICACHE_Init();
  MX_USB_PCD_Init();
  MX_SPI2_Init();
  MX_SPI3_Init();
  /* USER CODE BEGIN 2 */
  HAL_GPIO_WritePin(GPIOE,GPIO_PIN_7, GPIO_PIN_SET);

  //Powerup transceiver chip
  uint8_t command[8] = {0x02,0x01,0x00,0x01,0xC9,0xC3,0x80};
  HAL_GPIO_WritePin(GPIOD,GPIO_PIN_0, GPIO_PIN_RESET);
  HAL_SPI_Transmit(&hspi2,(uint8_t*)&command,7,100);
  HAL_GPIO_WritePin(GPIOD,GPIO_PIN_0, GPIO_PIN_SET);

  HAL_GPIO_WritePin(GPIOD,GPIO_PIN_0, GPIO_PIN_RESET);
  HAL_SPI_Receive(&hspi2, (uint8_t*)spi_buf,1,100);
  HAL_GPIO_WritePin(GPIOD,GPIO_PIN_0, GPIO_PIN_SET);

  //Check transceiver is on
  command[0] = 0x01;
  HAL_GPIO_WritePin(GPIOD,GPIO_PIN_0, GPIO_PIN_RESET);
  HAL_SPI_Transmit(&hspi2,(uint8_t*)&command,1,100);
  HAL_GPIO_WritePin(GPIOD,GPIO_PIN_0, GPIO_PIN_SET);

  HAL_GPIO_WritePin(GPIOD,GPIO_PIN_0, GPIO_PIN_RESET);
  HAL_SPI_Receive(&hspi2, (uint8_t*)spi_buf,9,100);
  HAL_GPIO_WritePin(GPIOD,GPIO_PIN_0, GPIO_PIN_SET);

  /* USER CODE END 2 */

  /* Infinite loop */
  /* USER CODE BEGIN WHILE */
  while (1)
  {
	  HAL_GPIO_WritePin(GPIOE,GPIO_PIN_7, GPIO_PIN_SET);
	  HAL_Delay(100);
	  HAL_GPIO_WritePin(GPIOE,GPIO_PIN_8, GPIO_PIN_SET);
	  HAL_Delay(100);
	  HAL_GPIO_WritePin(GPIOE,GPIO_PIN_9, GPIO_PIN_SET);
	  HAL_Delay(100);
	  HAL_GPIO_WritePin(GPIOE,GPIO_PIN_10, GPIO_PIN_SET);
	  HAL_Delay(100);
	  HAL_GPIO_WritePin(GPIOE,GPIO_PIN_11, GPIO_PIN_SET);
	  HAL_Delay(100);

	  HAL_GPIO_WritePin(GPIOE,GPIO_PIN_7, GPIO_PIN_RESET);
	  HAL_Delay(100);
	  HAL_GPIO_WritePin(GPIOE,GPIO_PIN_8, GPIO_PIN_RESET);
	  HAL_Delay(100);
	  HAL_GPIO_WritePin(GPIOE,GPIO_PIN_9, GPIO_PIN_RESET);
	  HAL_Delay(100);
	  HAL_GPIO_WritePin(GPIOE,GPIO_PIN_10, GPIO_PIN_RESET);
	  HAL_Delay(100);
	  HAL_GPIO_WritePin(GPIOE,GPIO_PIN_11, GPIO_PIN_RESET);
	  HAL_Delay(100);
    /* USER CODE END WHILE */

    /* USER CODE BEGIN 3 */
  }
  /* USER CODE END 3 */
}

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


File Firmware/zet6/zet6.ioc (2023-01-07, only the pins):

Mcu.UserName=STM32L562ZETx
PA11.Signal=USB_DM
PA12.Signal=USB_DP
PB13.Signal=SPI2_SCK
PB14.Signal=SPI2_MISO
PB15.Signal=SPI2_MOSI
PC10.Signal=SPI3_SCK
PC11.Signal=SPI3_MISO
PC12.Signal=SPI3_MOSI
PD0.Signal=GPIO_Output
PD8.Signal=GPIO_Output
PE10.Signal=GPIO_Output
PE11.Signal=GPIO_Output
PE7.Signal=GPIO_Output
PE8.Signal=GPIO_Output
PE9.Signal=GPIO_Output

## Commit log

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2021-10-02 Schematic v1.0.0
    Creation of KiCAD project file, initial draft of PCB schematic file, components chosen as a starting point and will likely be altered in future revisions.
    [MCU_L151CBT.sch, RF_CC1200.sch, Telemetry_KiCAD_Project.kicad_pcb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]
2021-10-02 Schematic v1.0.1
    Corrected page settings.
    [MCU_L151CBT.sch, RF_CC1200.sch, Telemetry_KiCAD_Project.sch]
2021-11-24 Included Amplifier, New Transceivers, Duplexer, and 37 Pin DSUB
    Still want to replace the microcontroller, will happen in next commit
    [37_Pin_DSUB_Bus.sch, ADL_Amplifier.sch, MCU_L151CBT.sch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]
2021-11-25 Replaced L151CBT with L552CC
    This is the same MCU as in the Data Collection board, should simplify testing and part ordering.
    A custom symbol was made and added to the RDT_Custom_Symbols library.
    [MCU_L151CBT.sch, MCU_L552CC.sch, Telemetry_KiCAD_Project.sch]
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2021-11-25 Correct SPI bus lines on main page
    [Telemetry_KiCAD_Project.sch]
2021-11-25 Added chip select functions for RX and TX chips
    The Si4463 datasheet mentions that some parameters can be quickly accessed if the chip select line is toggled
    [MCU_L552CC.sch, Telemetry_KiCAD_Project.sch]
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2021-11-25 I2C2 removed from MCU
    Carry over from copying the file from the Data Collection board
    [MCU_L552CC.sch]
2021-11-25 Corrected hierarchical pin directions, squashed bugs
    There are still some warnings about pins being connected but not driven, don't know how to fix those at the moment
    [37_Pin_DSUB_Bus.sch, ADL_Amplifier.sch, MCU_L552CC.sch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]
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2021-11-29 Replaced STM32L552 with STM32L562
    Now in a QFPN-100 package, lot's o' pins!
    [MCU_L552CC.sch, MCU_L562VE.sch, Telemetry_KiCAD_Project.sch]
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2021-12-01 Placed DB37 connector
    Might require some alignment later
    [Telemetry_KiCAD_Project.kicad_pcb]
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2021-12-03 Created separate schematics for chips acting in TX and RX
    Added link to document describing passive component selection
    [ADL_Amplifier.sch, Si4463.sch, Si4463_RX.sch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]
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2021-12-04 Added RSD Duplexer Footprint, rearranged RF matching networks
    [ADL_Amplifier.sch, MCU_L562VE.sch, RSD_Duplexer.sch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]
2021-12-04 PCB Layout Progress
    Everything appears to be connected...
    [DSUB-slot.sch, Telemetry_KiCAD_Project.kicad_pcb]
2021-12-04 Added RF trace clearances
    [Telemetry_KiCAD_Project.kicad_pcb]
2021-12-04 Added via fences to RF section, adjusted labels
    [Telemetry_KiCAD_Project.kicad_pcb]
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2021-12-04 Fixed unconnected ground pin on duplexer chip
    [Telemetry_KiCAD_Project.kicad_pcb]
2021-12-04 Fixed more unconnected ground pads
    [Telemetry_KiCAD_Project.kicad_pcb]
2021-12-06 Majorly Reorganized Project Directory
    This is done in an effort to help keep the repo organized and modularized.
    [37_Pin_DSUB_Bus.sch, 37_Pin_DSUB_Male.sch, ADL_Amplifier.sch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]
2021-12-06 Squashed commit of the following:
    commit dd5425a15ec90373b5e960bf340bab0c3bd07ece
    Merge: 8a575c8 cd97259
    Author: Thomas Francois <twfth9@mst.edu>
    Date: Sun Dec 5 21:38:26 2021 -0600
    Merge branch 'master' of https://github.com/MSTRocketDesignTeam/Avionics-Telemetry-PCB
    commit 8a575c872352ae5a3f01950cdc10612db62a8baa
    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
    [37_Pin_DSUB_Bus.sch, 37_Pin_DSUB_Male.sch, ADL_Amplifier.sch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]
2021-12-06 Added test points to main schematic page
    Also corrected library table
    [37_Pin_DSUB_Male.sch, Telemetry_KiCAD_Project.sch]
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2021-12-06 Fixed merge mistakes between branches
    [37_Pin_DSUB_Male.sch, Telemetry_KiCAD_Project.sch]
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2021-12-19 Updated DSUB connector assignments
    Welp, looks like everything got turned upside down, time to flip everything on the board, ugh
    [ADL_Amplifier.sch, DSUB-37_Male.sch, MCU_L562VE.sch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]
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2021-12-20 Arranged TX and RX SPI busses
    It just occurred to me that I could just swap the TX and RX SPI busses and routing would be 1000% easier. D'oh!
    [MCU_L562VE.sch, RSD_Duplexer.sch, Telemetry_KiCAD_Project.kicad_pcb]
2021-12-20 Swapped SPI2 and SPI3 for TX/RX chips
    [MCU_L562VE.sch, Telemetry_KiCAD_Project.sch]
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2021-12-20 Reworked RX SPI lines
    [Telemetry_KiCAD_Project.kicad_pcb]
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2021-12-20 Tidied up remaining ratsnest lines
    Version 2 complete
    [Telemetry_KiCAD_Project.kicad_pcb]
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2021-12-20 Added copper pours, removed filled zones around RF section
    [Telemetry_KiCAD_Project.kicad_pcb]
2022-01-17 Major Redesign
    - Copper ground pours on F and B.
    - Improved isolation between data lines
    - Expanded via fences around RF section.
    - GND plane isolation peninsulas for crystals.
    - Simplified I2C, SPI, and USB lines for reduced interference.
    - Added 3D models for all components.
    - Adjusted positions of RF components for improved impedance matching.
    - RF components to 0402 package from 0603 for improved impedance matching.
    - Traces for RF section have rounded corners to help improve impedance matching and reduce interference.
    - Moved silkscreen labels to outside via fence for improved legibility.
    - Improved trace thicknesses for power delivery.
    - Updated libraries to include those f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
    [37_Pin_DSUB_Bus.sch, 37_Pin_DSUB_Male.sch, ADL_Amplifier.sch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]
2022-01-17 Fixed some unconnected GND stitching vias
    [Telemetry_KiCAD_Project.kicad_pcb]
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2022-01-17 Corrected TX/RX crystal grounds
    [Telemetry_KiCAD_Project.kicad_pcb]
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2022-01-18 Updated PCB edge silkscreen and rounded edge cuts corner on DSUB side
    [Telemetry_KiCAD_Project.kicad_pcb]
2022-01-18 added qr code
    qr code was added to the board on the back silkscreen
    [Telemetry_KiCAD_Project.kicad_pcb]
2022-01-18 Adjusted position of USB connector and components, length matched data lines
    [Telemetry_KiCAD_Project.kicad_pcb]
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2022-01-19 Updated crystal footprints, added 3D model
    PCB layout now invalid, changes pending
    [MCU_L562VE.sch, RSD_Duplexer.sch, Si4463_RX.sch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]
2022-01-19 Added larger crystals to TX/RX and MCU chips
    [Telemetry_KiCAD_Project.kicad_pcb]
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2022-01-19 Corrected jumper on MCU sheet
    [MCU_L562VE.sch]
2022-01-19 Corrected center pin of RSD chip footprint
    [RSD_Duplexer.sch, Telemetry_KiCAD_Project.kicad_pcb]
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2022-01-21 Adapted layout to different linear regulator for USB
    [MCU_L562VE.kicad_sch, Si4463_RX.kicad_sch, Si4463_TX.kicad_sch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]
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2022-02-25 Adjusted some trace thicknesses, added more vias to USB voltage regulator
    [Telemetry_KiCAD_Project.kicad_pcb]
2022-02-28 Corrected microcontroller component sheet
    [MCU_L562VE.kicad_sch, Telemetry_KiCAD_Project.kicad_sch]
2022-02-28 Adjusted edge cuts, aligned silkscreen, center hole, all components
    Some traces still need to be adjusted, i.e. status LEDs
    [Telemetry_KiCAD_Project.kicad_pcb]
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2022-02-28 Corrected edge cuts
    [Telemetry_KiCAD_Project.kicad_pcb]
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2022-03-02 Increased spacing around MCU, added filter caps for SMPS, rerouted 5V from DSUB, changed SMA to right angle
    [MCU_L562VE.kicad_sch, Telemetry_KiCAD_Project.kicad_pcb, Telemetry_KiCAD_Project.kicad_sch]
2022-03-02 Added male sma model to coax connector for assisting in alignment
    [Telemetry_KiCAD_Project.kicad_pcb]
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2022-03-23 Adjusted 5V lines, corrected ground fences, added cutout for USB connector
    [Telemetry_KiCAD_Project.kicad_pcb, Telemetry_KiCAD_Project.kicad_sch, USB_ESD.kicad_sch]
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2022-03-26 Changed D1 LCSC to make component fit on pads
    [USB_ESD.kicad_sch]
2022-08-19 Added more JLC part numbers and added missing voltage regulator connection
    [MCU_L562VE.kicad_sch, Si4463_RX.kicad_sch, Si4463_TX.kicad_sch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]
2022-08-19 edited routing, added more jlc part numbers, organized files, and regenerated production files
    [TelemetryBoardBOM.csv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]
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2022-08-27 Added resistor that was missing, connected a resistor that was floating, and updated LCSC numbers
    [MCU_L562VE.kicad_sch, TelemetryBoardBOM.csv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]
2022-08-27 Fixed incorrect LCSC numbers
    [ADL_Amplifier.kicad_sch, MCU_L562VE.kicad_sch, Si4463_TX.kicad_sch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]
2022-11-06 Updated DSUB model and generated STEP model of board
    [Telemetry_KiCAD_Project.kicad_pcb, USB_ESD.kicad_sch]
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2022-11-10 fixed board update issue by renaming usb pin 0 and DSUB pin 0
    [DSUB-37_Male.kicad_sch, Telemetry_KiCAD_Project.kicad_pcb, USB_ESD.kicad_sch]
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2022-11-11 fixed weird routing
    [Telemetry_KiCAD_Project.kicad_pcb]
2022-11-12 tried to minimize loops and traces under the IC
    [Telemetry_KiCAD_Project.kicad_pcb]
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2022-11-28 Rerouted some stuffs, close to final for Rev 3
    [MCU_L562VE.kicad_sch, Telemetry_KiCAD_Project.kicad_pcb, Telemetry_KiCAD_Project.kicad_sch]
2022-12-11 Moved voltage regulator down to make room for the case
    [Telemetry_KiCAD_Project.kicad_pcb]
2022-12-11 Moved voltage regulator down to make room for the case and cleaned up some routing
    [Telemetry_KiCAD_Project.kicad_pcb]
2022-12-11 Fixed git errors
    [Telemetry_KiCAD_Project.kicad_pcb]
2022-12-11 Adjusted RF fences, tuned USB trace lengths, adjusted GND pours
    [Telemetry_KiCAD_Project.kicad_pcb]
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2022-12-11 Split the case step file into the lid and case
    [PCB_Case.step, PCB_Case_Body.step, PCB_Case_Top.step]
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2022-12-14 Corrected USB footprint and moved USB edge cut
    [Telemetry_KiCAD_Project.kicad_pcb, Telemetry_KiCAD_Project.kicad_sch, USB_ESD.kicad_sch]
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2022-12-31 Changed SPI debug headers to be a proper header component. Updated 3D model
    [Telemetry_KiCAD_Project.kicad_pcb, Telemetry_KiCAD_Project.kicad_sch]
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2023-01-02 reset capacitor routing from underneath switch
    [Telemetry_KiCAD_Project.kicad_pcb]
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2023-01-04 Regenerated gerbers, refilled zones, and wrote firmware that causes leds to blink in sequence.
    [Telemetry_KiCAD_Project-3_3V_Cu.gbr, Telemetry_KiCAD_Project-B_Cu.gbr, Telemetry_KiCAD_Project-B_Mask.gbr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]
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

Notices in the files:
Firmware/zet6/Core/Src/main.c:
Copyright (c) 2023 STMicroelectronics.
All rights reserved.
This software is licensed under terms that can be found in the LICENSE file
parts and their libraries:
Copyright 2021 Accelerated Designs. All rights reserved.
